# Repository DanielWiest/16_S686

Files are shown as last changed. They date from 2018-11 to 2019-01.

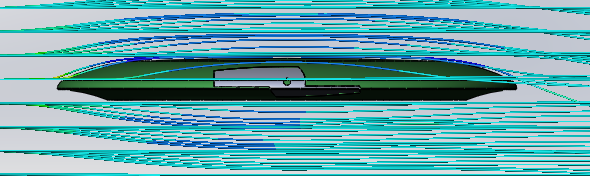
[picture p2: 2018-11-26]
Multimedia/Simulation_Renders/Port_Closed_Streamlines.PNG

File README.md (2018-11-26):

# __**16.S686**__ Closed Loop Frisbee Control
### A Repository of Code, Relevant Documents, and CAD Files

Frisbee Airflow

Surface Velocity

See subsections for more details.

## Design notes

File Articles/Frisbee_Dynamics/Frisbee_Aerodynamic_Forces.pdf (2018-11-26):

Physics 382, Student (2016) | Advanced Lab | v3.3, p.1

### Aerodynamics Forces on Frisbee

Karl Prasher and Professor Martin Madsen

Wabash College, 301 W. Wabash Ave, Crawfordsville, IN 47933

| (Dated: May 5, 2016)

The initial idea of the ultimate frisbee disc was first invented by Fred Morrison

in 1938 when him and his wife were tossing around an empty cake pan. Over the

years, Morrison developed several prototypes which eventually became the modern-

day ultimate disc. Richard Feynman modeled the disc as a ”wobbling plate” to

describe the motion of the frisbee [6]. The purpose of this experiment wasn’t to

model the motion of the disc but describe and explain the forces on a frisbee with

air drag.

I. INTRODUCTION

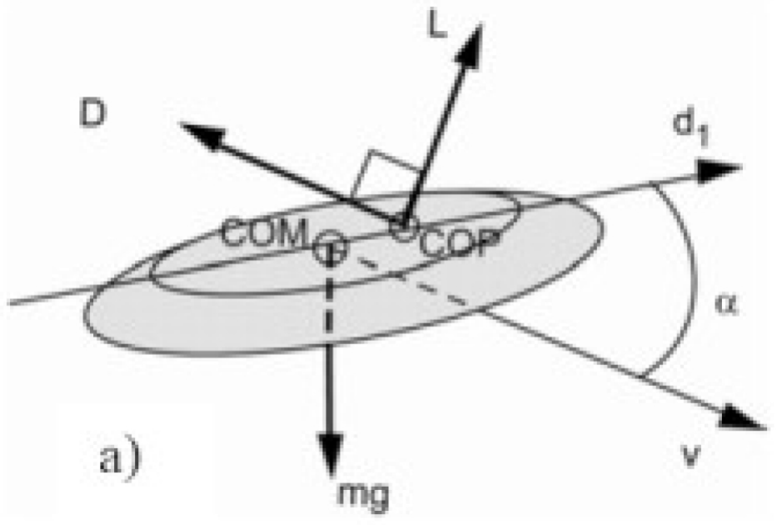
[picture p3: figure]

FIG. 1: This figure shows the setup procedure used during this experiment.

Richard Feynman once modeled the rotation and motion of a ”wobbling disc” similar

to an ultimate frisbee. He took moment of inertia, angular velocity, and angle of attack

into account. This model was just to describe the motion. This experiment took a different

approach and wanted to model the force on the frisbee changing the angle of attack therefore

changing the surface area as the frisbee travels through the air shown by Fig. . To model

the frisbee traveling through the air, a wind tunnel was built with a chamber able to insert

a pivot arm attached to the frisbee. Instead a modern-day 175 gram frisbee, we used an

mini-frisbee weighting approximately 28 grams.

II. SETUP

Fig. 2 shows the initial position of the system being tested. The initial trials began with

the pivot arm being at 90 degrees with relation to the x-axis. As the experiment continued,

the angle of the pivot arm was changed with respect to the x-axis called the attack angle.

Therefore, the surface area of the frisbee was changed ultimately changing the force on the

disc.

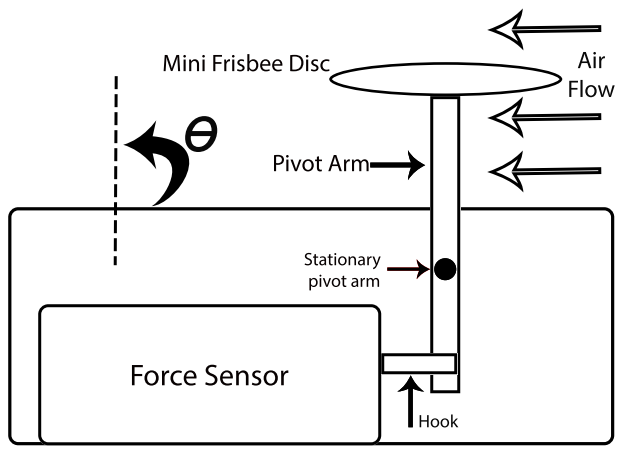
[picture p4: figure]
ForceSensor; MiniFrisbeeDisc; Stationary pivotarm; Air Flow; Hook; PivotArm

FIG. 2: This figure shows the setup procedure used during this experiment.

III. MODEL

Initially, the model relied on the rotation of the disc. Practicality though, there were

problems with a spinning disc inside the test chamber. Enabling the spinning motion was

not the problem, but measuring the force on the pivot arm while the disc was spinning was

the problem. It was not practical in my initial setup so the only variables that were changed

were the voltage powering the fan and the angle of attack. Then from Morrison’s paper, his

model was

Ftotal = Fdrag + Flif t, | (1)

but this experiment did not have the proper equipment to measure to the Lift Force so we

were left with only the Drag Force. Therefore my model came out to be

Fdrag = −

CDρAv²
2
, | (2)

where ρ is the density of air which is constant for this experiment, CD is a coefficient

determined by the physical attributes of the frisbee, and v is the velocity of the frisbee.

This follows the previous groups work that the model of the drag force should be close to a

quadratic fit model.

IV. DATA

My first task was to collect data over the same object as the previous group. By doing

this, it ensures that the equipment and model are up-to-date and works shown by Fig. 3.

This is shown in the analysis section with the curve fit.

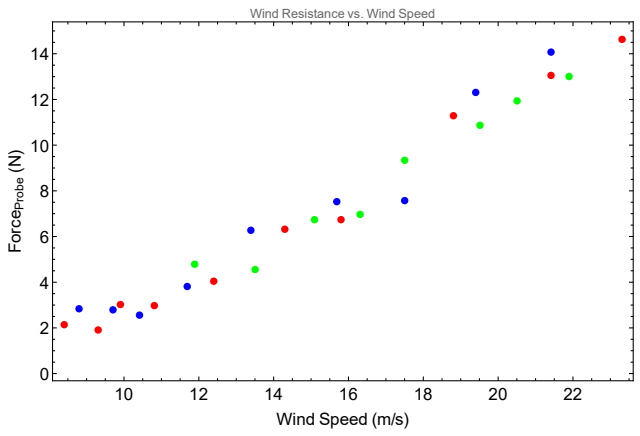
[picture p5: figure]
Wind Speed (m/s); ForceProbe (N); Wind Resistance vs. Wind Speed

FIG. 3: This plot shows the raw data over three trials of measuring the force upon the

racquetball.

Wind Resistance vs. Wind Speed on Mini Frisbee

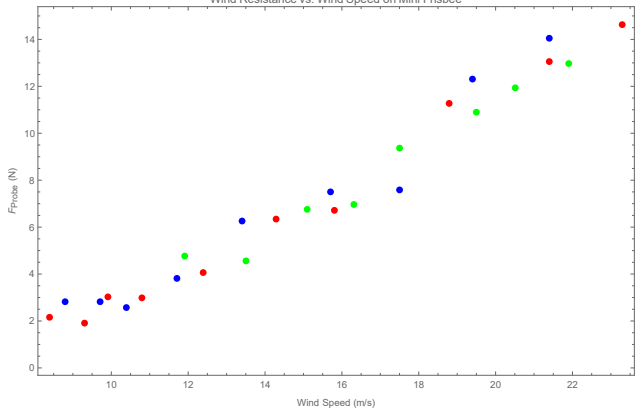
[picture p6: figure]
Wind Speed (m/s); FProbe (N)

FIG. 4: This plot shows the raw data over three trials of measuring the force upon the

mini frisbee.

Shown in Fig. 4, the data from the mini frisbee at 90 degrees was collected. During

those trials, only the voltage was changing. This shows a similar relationship of the force on

the mini frisbee as the racquetball. They both follow a parametric equation and this makes

sense with such a small cross-sectional area of the mini frisbee when it is as 90 degrees.

V. ANALYSIS

Based off Fig. 6, we were able to establish a clear relationship between the force of the

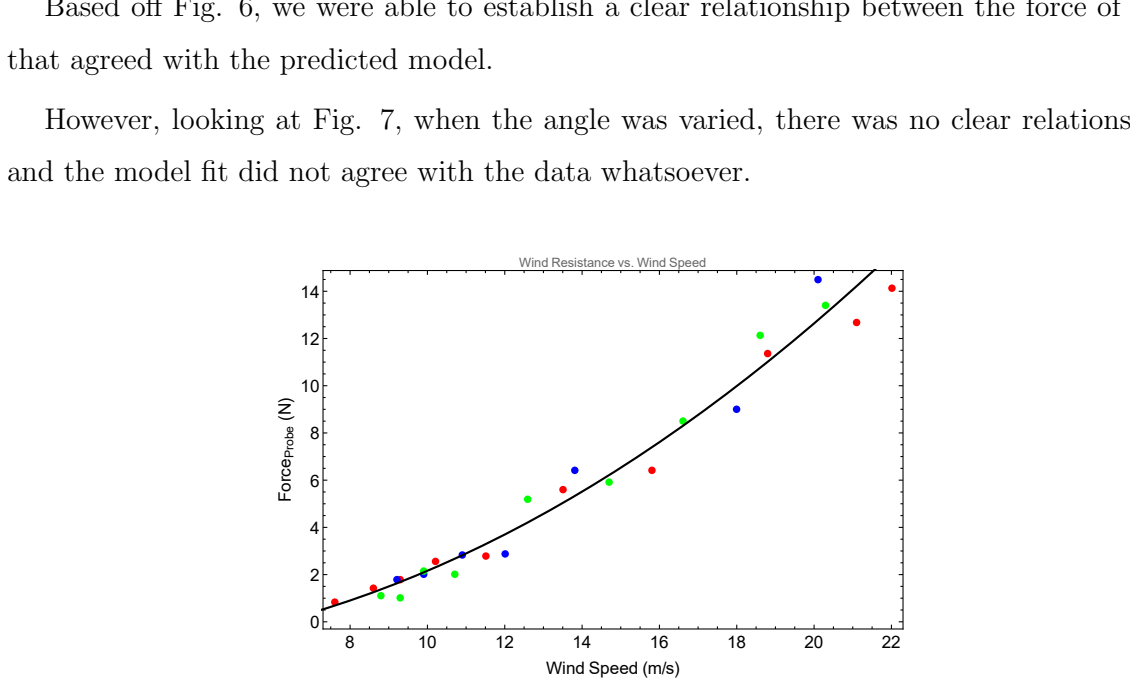
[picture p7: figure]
that agreed with the predicted model.; Wind Speed (m/s); ForceProbe (N); Wind Resistance vs. Wind Speed

However, looking at Fig. 7, when the angle was varied, there was no clear relationship

and the model fit did not agree with the data whatsoever.

FIG. 5: This plot shows the raw data over three trials of measuring the force upon the

racquetball.

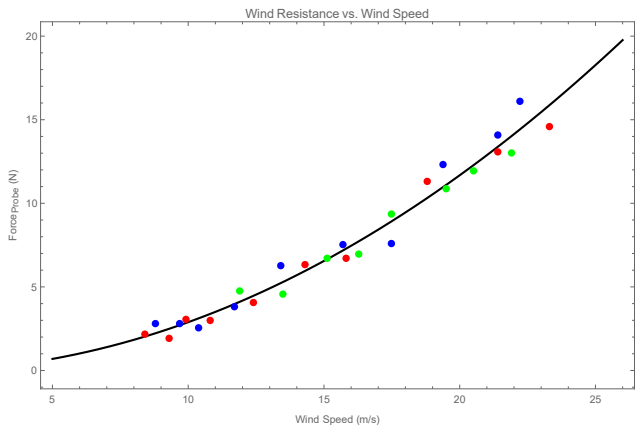
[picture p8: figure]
Wind Speed (m/s); ForceProbe (N); Wind Resistance vs. Wind Speed

FIG. 6: This plot shows a model with the three data sets of measuring the force upon the

mini frisbee.

74 | 76 | 78 | 80 | 82 | 84 | 86

2.0

2.2

2.4

2.6

2.8

3.0

Angle

FProbe on Mini Frisbee

{Angle of Attack vs. Force on Probe}

FIG. 7: This plot shows the raw data and model of measuring the drag force upon the

frisbee as the angle of attack was varied.

VI. CONCLUSION

Based on Fig. 6, a clear relationship between the Drag Force and the wind speed is

present but when the angle of attack of the frisbee (changing the cross sectional area of the

mini frisbee) is changed, there appears to be no relationship whatsoever. This could be due

to the setup of the mini frisbee yielding unreadable results. Further work should be done to

include the lift portion of the proper model of the total force on a rotating disc.

ACKNOWLEDGMENTS

We acknowledge the help and support of the Wabash College Physics Department.

[1] Baumback, K. “The Aerodynamics of Frisbee Flight.” Undergraduate Journal of Mathematical

Modeling: One Two UJMM: One Two, 3(1). (2013).

[2] Hubbard, M., & Cheng, K. B. “Optimal discus trajectories”. Journal of Biomechanics, 40(16),

3650-3659. (2007).

[3] Hummel, S. A. “Frisbee flight simulation and throw biomechanics.” (2003)
[4] Morrison, V. R. “The Physics of Frisbees.” Mount Allison University. (2005).
[5] Motoyama, E. “The Physics of Flying Discs.” (2002).

[6] Feynman, R.P. ”Surely You’re Joking, Mr. Feynman!”, New York: W. W. Norton, 1985 pp.

157158.

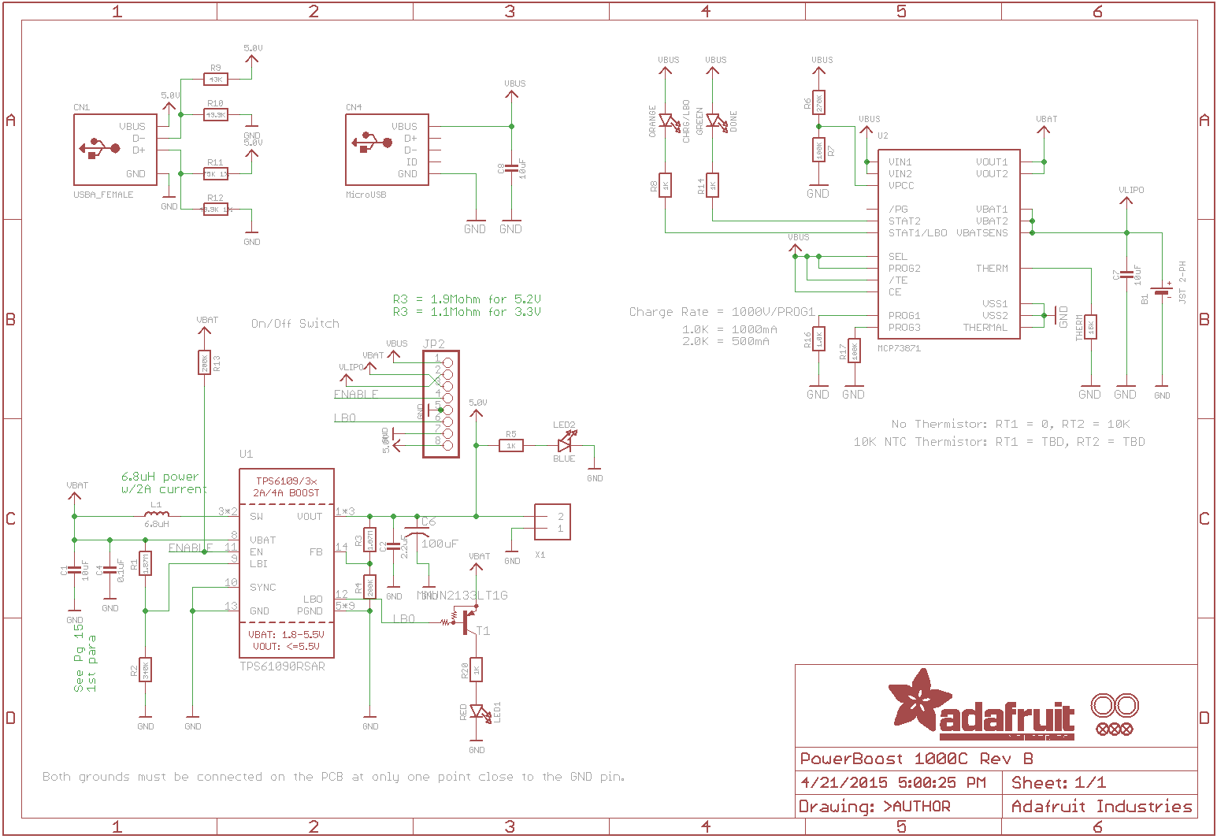
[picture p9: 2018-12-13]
Documents/PartSchematics/Powerboost.png

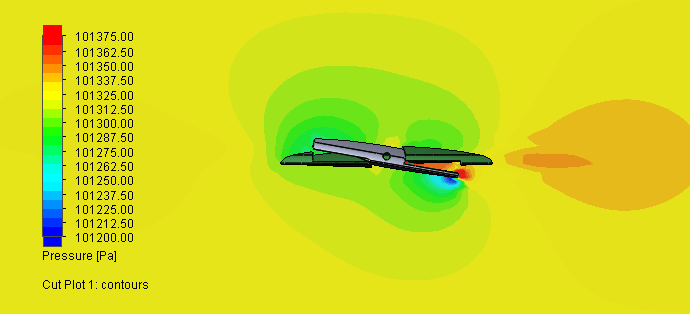
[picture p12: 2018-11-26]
Multimedia/Simulation_Renders/Port_Open_Pressure_Distribution.PNG

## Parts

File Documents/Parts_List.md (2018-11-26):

# Parts List

### 1. Solenoid Actuator:
Solenoid

Available [here](https://www.adafruit.com/product/2776) $4.95

### 2. Teensy 3.6 Microcontroller:
Teensy

Available [here](https://www.adafruit.com/product/3266) $29.95

### 3. Battery Charging and Voltage Regulation:
Boost + Regulator

Available [here](https://www.adafruit.com/product/2465) $19.95

### 4. Lithium Polymer Battery (500 mAh):
Battery

Available [here](https://www.adafruit.com/product/1578) $7.95

### 5. Hyperion High Speed Servo Actuator:
Hyperion Servo

Available [here](https://hyperion-world.com/en/p1772889-hp-ds09-gmd-14179) $11.86

### 6. Hyperion Servo Programming Adapter:
Programming Lead

Available [here](https://hyperion-world.com/en/p1770829-hp-at-prgusb) $13.90

### 7. Frisbee:
Frisbee

Available [here](https://www.amazon.com/Innova-Beast-Golf-Disc-Colors/dp/B00611XYXM) $13.90

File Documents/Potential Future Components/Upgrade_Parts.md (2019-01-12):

# Parts List

### SERVO Saver:


The impact of hitting the ground would likely strip the servo's gearing without any sort of protection.

Available [here](https://www.amazon.com/Hot-Racing-SHS88H-Aluminum-Vehicle/dp/B00A29B2D8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)

### 2. Teensy 3.6 Microcontroller:

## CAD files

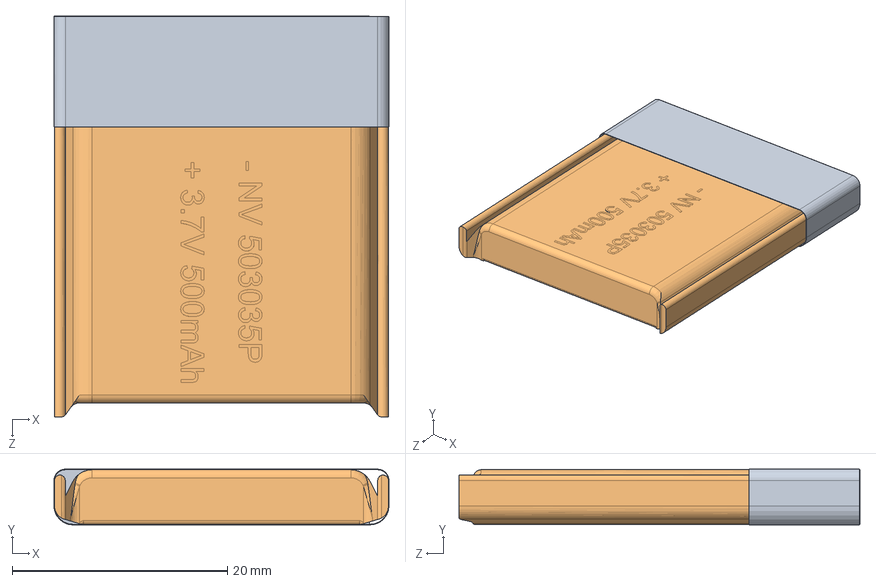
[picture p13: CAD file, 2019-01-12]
CAD/Battery/500mAh Battery.SLDASM
31.1 x 5.17 x 37.2 mm
Kapton Tape
Battery Cell
Board Part 1
PCB
Board Part 2

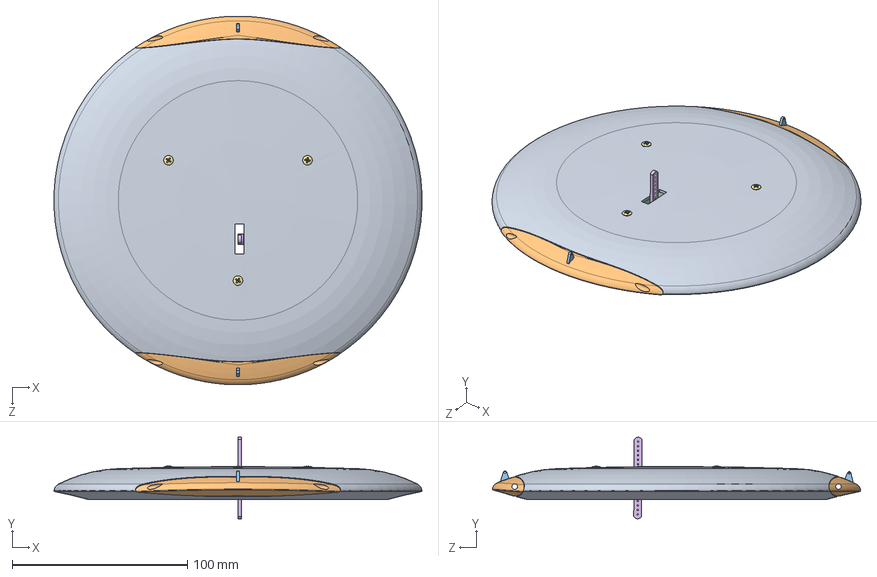
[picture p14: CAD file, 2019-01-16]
CAD/TopLevelAllComponents.SLDASM
209.8 x 46.5 x 210.0 mm
Frisbee_with_control_cutout_linear_v2
linear_control_surface_v1 x 2
ControlHorn x 2
Kapton Tape
Battery Cell
Board Part 1
PCB
Board Part 2
Adafruit_BNO055
Teensy 3.6
PowerBoost1000C
ElectronicsEnclosure
DS09GMD
long_control_horn
oval head_am x 3

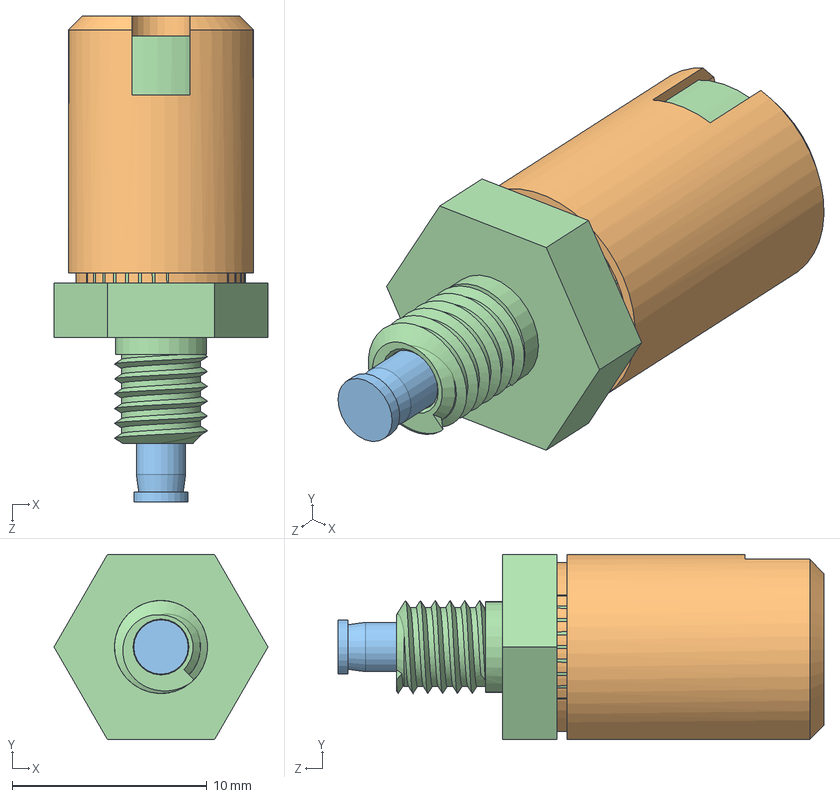
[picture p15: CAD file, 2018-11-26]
CAD/Solenoids/Solenoid_CAD_alternative_option.sldasm
11.0 x 9.53 x 25.0 mm
SPRING_Default
HOUSING_Default
PLUNGER_Default
Swing bolt_Default

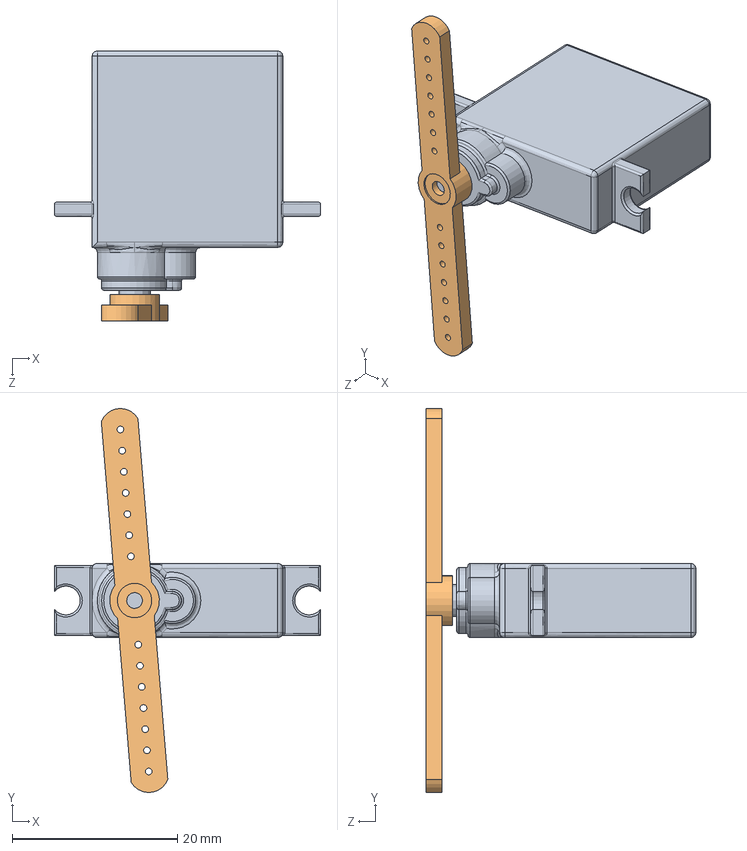
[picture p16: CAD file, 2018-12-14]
CAD/Servo/ServoAssem.SLDASM
32.2 x 46.4 x 32.6 mm
DS09GMD
long_control_horn

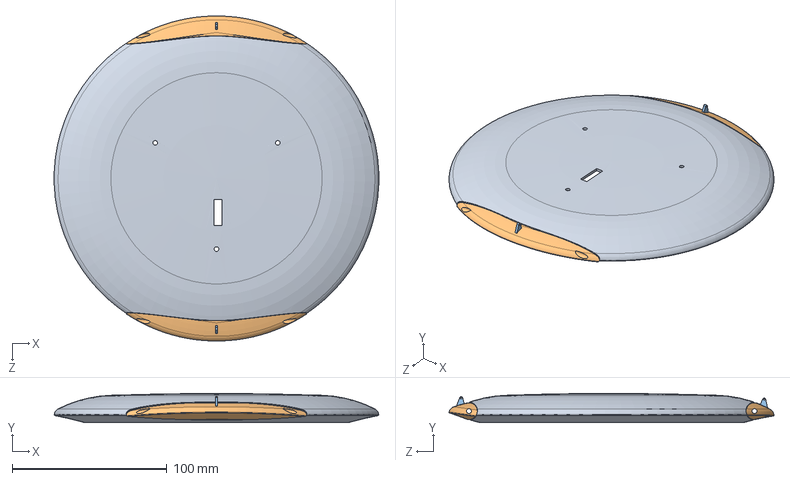
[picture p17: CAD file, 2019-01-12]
CAD/Top_level_assembly_v2.SLDASM
209.8 x 18.8 x 210.0 mm
Frisbee_with_control_cutout_linear_v2
linear_control_surface_v1 x 2
ControlHorn x 2

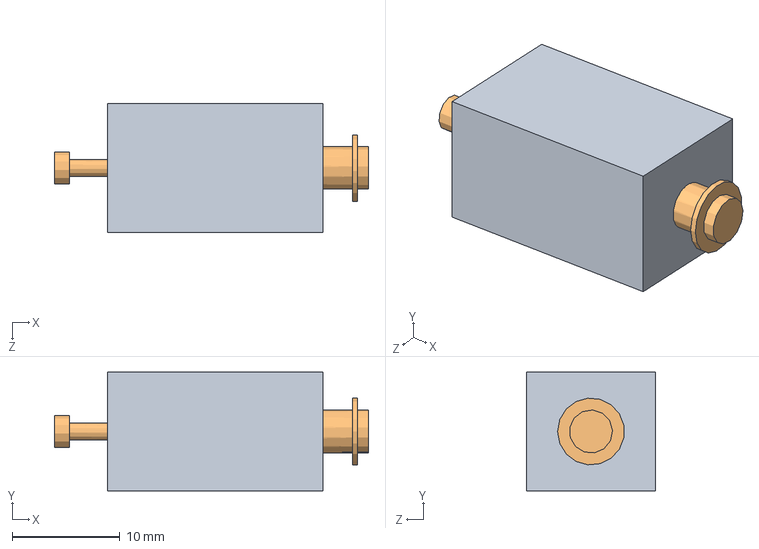
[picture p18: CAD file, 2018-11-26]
CAD/Solenoids/microSolenoidAssembly.SLDASM
29.1 x 11.0 x 12.0 mm
Pin

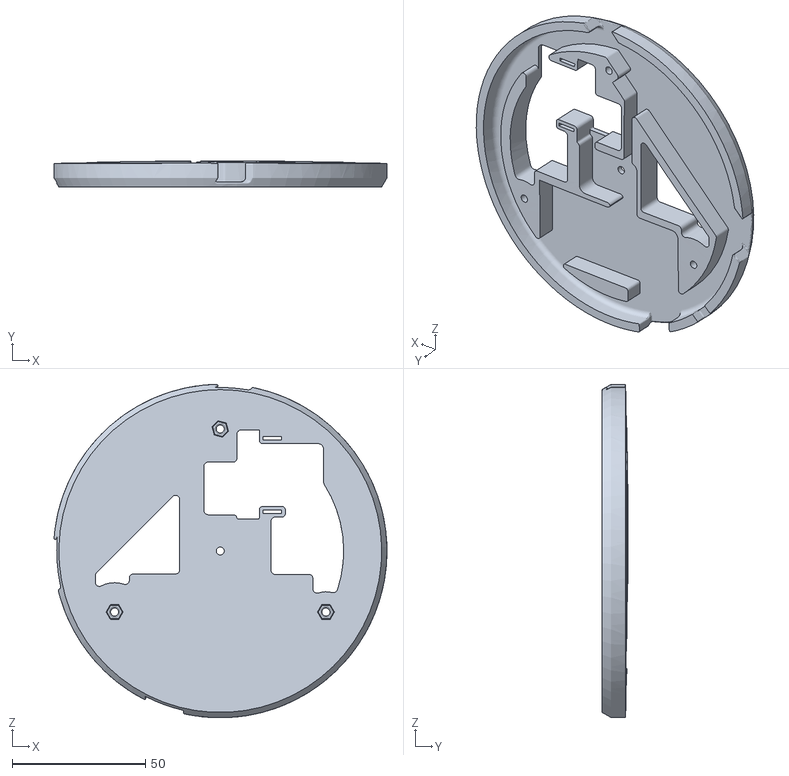
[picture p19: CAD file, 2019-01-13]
CAD/3D Printing Files/ElectronicsEnclosureTEST.STL
124.8 x 9.85 x 124.9

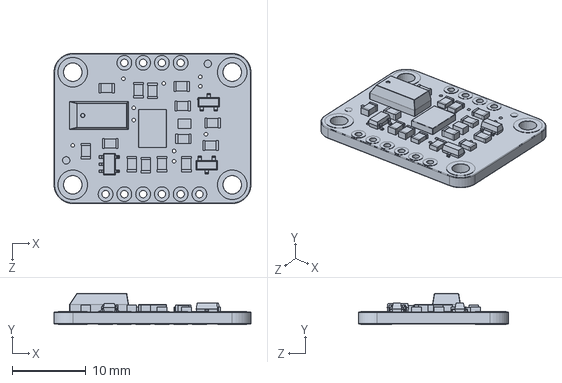
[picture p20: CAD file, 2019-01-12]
CAD/BNO005/Adafruit_BNO055.SLDPRT
26.7 x 4.20 x 20.3 mm

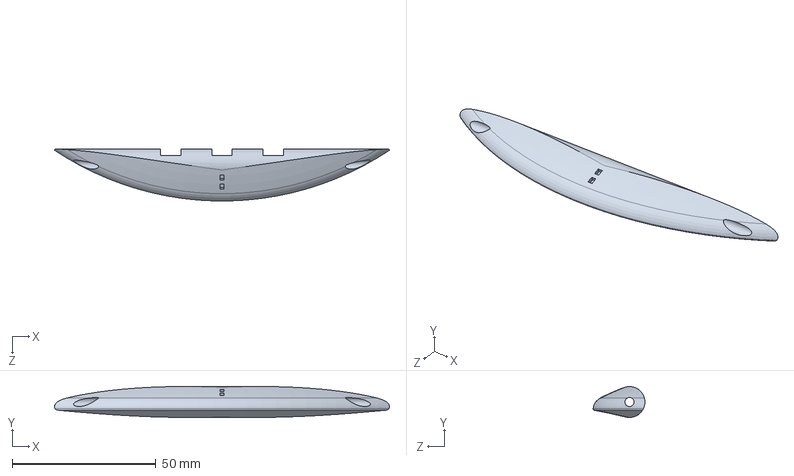
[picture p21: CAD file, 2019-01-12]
CAD/Control_Surfaces/linear_control_surface_v1.sldprt
116.7 x 10.8 x 18.1 mm

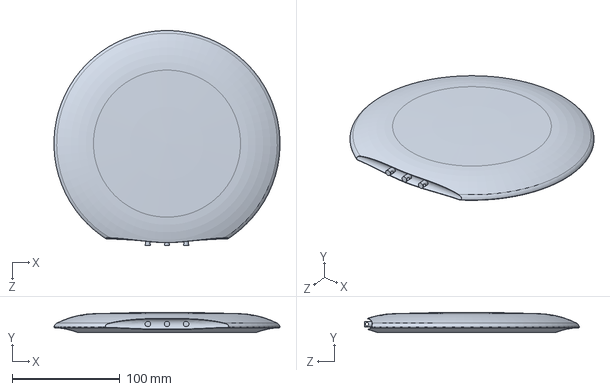
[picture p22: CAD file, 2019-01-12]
CAD/Frisbee/Frisbee_with_control_cutout_linear_v2.SLDPRT
209.8 x 18.8 x 199.4 mm

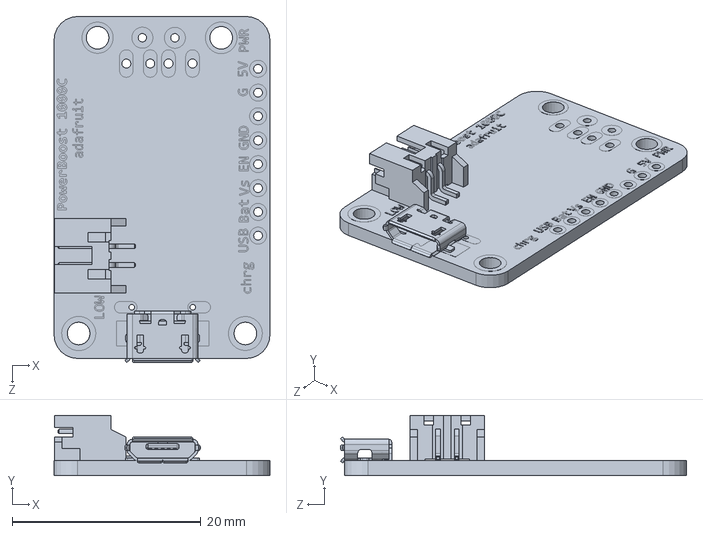
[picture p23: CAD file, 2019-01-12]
CAD/PowerBoost 1000C/PowerBoost1000C.SLDPRT
22.9 x 6.39 x 36.6 mm

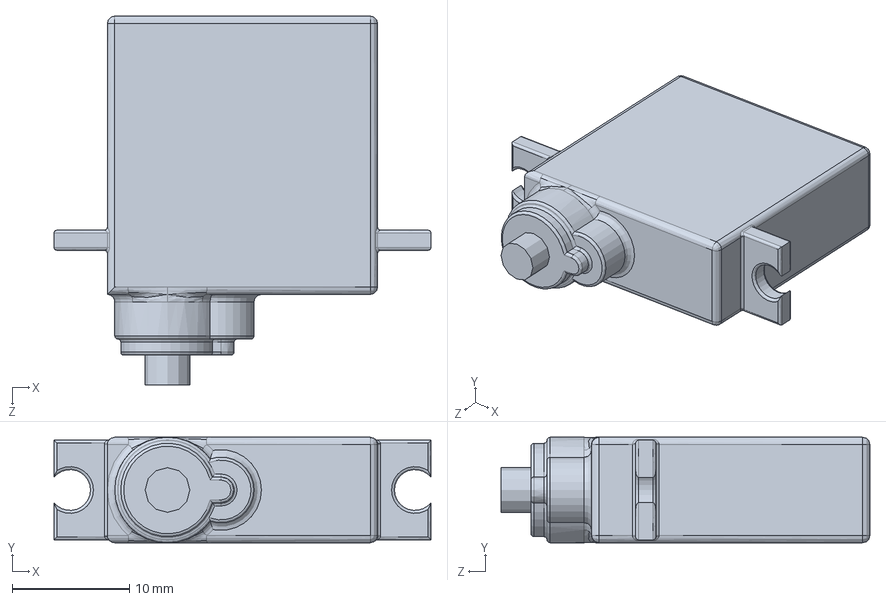
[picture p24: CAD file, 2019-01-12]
CAD/Servo/DS09GMD.SLDPRT
32.2 x 9.00 x 31.5 mm

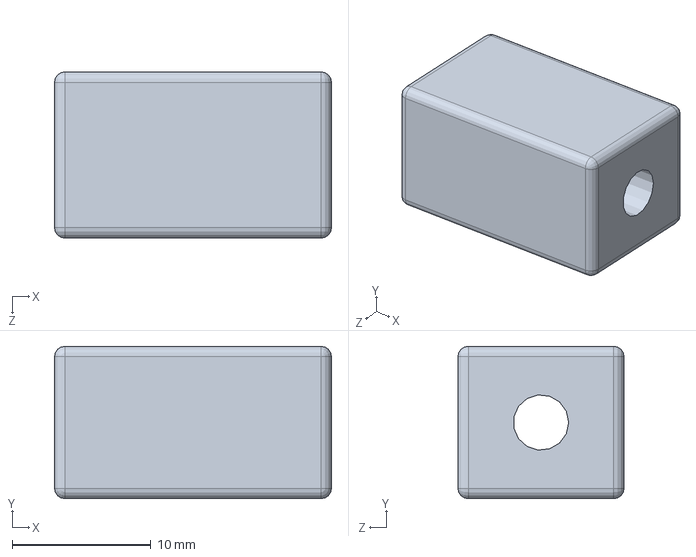
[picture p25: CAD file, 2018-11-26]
CAD/Solenoids/Body.SLDPRT
20.0 x 11.0 x 12.0 mm

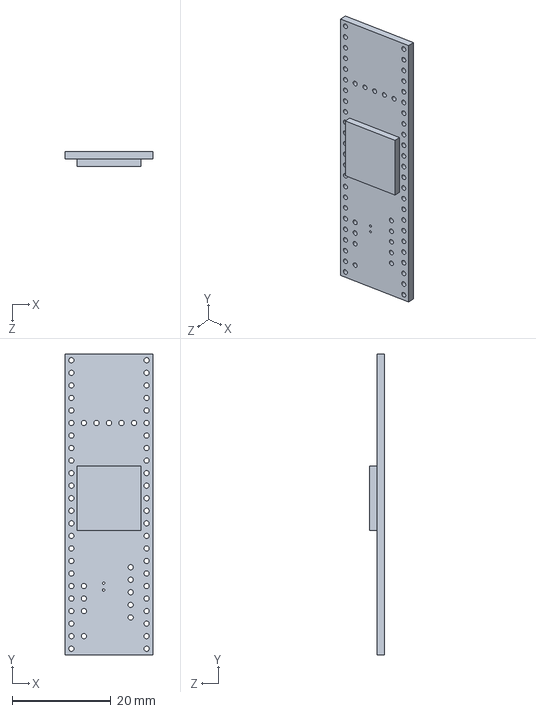
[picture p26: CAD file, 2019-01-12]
CAD/Teensy/Teensy 3.6.SLDPRT
17.8 x 61.0 x 3.10 mm

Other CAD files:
CAD/Battery/Battery Cell.sldprt
CAD/Control_Surfaces/ControlHorn.sldprt
CAD/ElectronicsEnclosure.sldprt
CAD/Frisbee/Unaltered_disc.SLDPRT
CAD/Battery/Board Part 1.sldprt
CAD/Battery/Board Part 2.sldprt
CAD/Battery/Kapton Tape.sldprt
CAD/Battery/PCB.sldprt
CAD/Control_Surfaces/Control_surface_v2.sldprt
CAD/Frisbee/Frisbee_with_control_cutout.SLDPRT
CAD/Servo/long_control_horn.SLDPRT
CAD/Solenoids/Pin.SLDPRT
CAD/Top_level_assembly.SLDASM

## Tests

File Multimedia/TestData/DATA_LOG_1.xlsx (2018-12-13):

Time | Euler_x | Euler_y | Euler_z | Grav_x | Grav_y | Grav_z | LinAcc_x | LinAcc_y | LinAcc_z | Control_Setpoint
1234 | 0 | 0 | 0 | 0 | 0 | 0 | 0 | 0 | 0 | 0
1245 | 2.75 | 5.44 | -2.12 | 0.93 | 0.36 | 9.75 | -4.1 | -1.98 | -2.69 | 0
1256 | 3.25 | 6.62 | -2.88 | 1.13 | 0.49 | 9.72 | -4.27 | -1.76 | -3.52 | 0
1267 | 3.88 | 8 | -3.94 | 1.37 | 0.67 | 9.68 | -4.13 | -1.47 | -3.78 | 0
1282 | 4.56 | 9.56 | -5.31 | 1.63 | 0.89 | 9.62 | -3.22 | -0.76 | -2.7 | 0
1293 | 5.25 | 11.19 | -6.81 | 1.91 | 1.14 | 9.54 | -2.37 | -0.78 | -1.01 | 0
1305 | 6.69 | 14.56 | -10 | 2.47 | 1.65 | 9.34 | -2.22 | -0.83 | -0.41 | 0
1316 | 7.38 | 16.25 | -11.44 | 2.74 | 1.87 | 9.22 | -1.21 | -1.07 | 1.06 | 0
1327 | 8 | 17.81 | -12.62 | 3 | 2.04 | 9.1 | -1.08 | -1.26 | 1.6 | 0
1338 | 8.5 | 19.31 | -13.69 | 3.24 | 2.19 | 8.98 | -1.29 | -1.29 | 1.65 | 0
1353 | 9.06 | 20.69 | -14.62 | 3.47 | 2.31 | 8.87 | -1.55 | -1.06 | 0.02 | 0
1365 | 10.06 | 23.44 | -16.69 | 3.9 | 2.59 | 8.61 | -1.56 | -1.01 | 0.2 | 0
1377 | 10.62 | 24.75 | -18 | 4.1 | 2.76 | 8.46 | -1.43 | -1.03 | 0.65 | 0
1389 | 11.12 | 25.94 | -19.5 | 4.29 | 2.95 | 8.3 | -1.13 | -1.03 | 1.37 | 0
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

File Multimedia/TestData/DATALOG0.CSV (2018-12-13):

Time | Euler_x | Euler_y | Euler_z | Grav_x | Grav_y | Grav_z | LinAcc_x | LinAcc_y | LinAcc_z | Control_Setpoint
1143 | 0.00 | 0.00 | 0.00 | 0.00 | 0.00 | 0.00 | 0.00 | 0.00 | 0.00 | 0.00
1154 | 0.00 | 0.00 | 0.00 | 0.00 | 0.00 | 0.00 | 0.00 | 0.00 | 0.00 | 0.00
1166 | 0.00 | 0.00 | 0.00 | 0.00 | 0.00 | 0.00 | 0.00 | 0.00 | 0.00 | 0.00
1177 | 0.00 | 0.00 | 0.00 | 0.00 | 0.00 | 0.00 | 0.00 | 0.00 | 0.00 | 0.00
1289 | 0.00 | 0.00 | 0.00 | 0.00 | 0.00 | 0.00 | 0.00 | 0.00 | 0.00 | 0.00
1300 | 0.00 | 0.00 | 0.00 | 0.00 | 0.00 | 0.00 | 0.00 | 0.00 | 0.00 | 0.00
1312 | 0.00 | 0.00 | 0.00 | 0.00 | 0.00 | 0.00 | 0.00 | 0.00 | 0.00 | 0.00
1324 | 0.00 | 0.00 | 0.00 | 0.00 | 0.00 | 0.00 | 0.00 | 0.00 | 0.00 | 0.00
1335 | 0.00 | 0.00 | 0.00 | 0.00 | 0.00 | 0.00 | 0.00 | 0.00 | 0.00 | 0.00
1346 | 0.00 | 0.00 | 0.00 | 0.00 | 0.00 | 0.00 | 0.00 | 0.00 | 0.00 | 0.00
1358 | 0.00 | 0.00 | 0.00 | 0.00 | 0.00 | 0.00 | 0.00 | 0.00 | 0.00 | 0.00
1369 | 0.00 | 0.00 | 0.00 | 0.00 | 0.00 | 0.00 | 0.00 | 0.00 | 0.00 | 0.00
1383 | 0.00 | 0.00 | 0.00 | 0.00 | 0.00 | 0.00 | 0.00 | 0.00 | 0.00 | 0.00
1394 | 0.00 | 0.00 | 0.00 | 0.00 | 0.00 | 0.00 | 0.00 | 0.00 | 0.00 | 0.00
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

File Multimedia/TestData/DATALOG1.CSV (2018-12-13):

Time | Euler_x | Euler_y | Euler_z | Grav_x | Grav_y | Grav_z | LinAcc_x | LinAcc_y | LinAcc_z | Control_Setpoint
1949 | 0.00 | 0.00 | 0.00 | 0.00 | 0.00 | 0.00 | 0.00 | 0.00 | 0.00 | 0.00
1961 | 0.00 | 0.00 | 0.00 | 0.00 | 0.00 | 0.00 | 0.00 | 0.00 | 0.00 | 0.00
1973 | 0.00 | 0.00 | 0.00 | 0.00 | 0.00 | 0.00 | 0.00 | 0.00 | 0.00 | 0.00
1984 | 0.00 | 0.00 | 0.00 | 0.00 | 0.00 | 0.00 | 0.00 | 0.00 | 0.00 | 0.00
1996 | 0.00 | 0.00 | 0.00 | 0.00 | 0.00 | 0.00 | 0.00 | 0.00 | 0.00 | 0.00
2008 | 0.00 | 0.00 | 0.00 | 0.00 | 0.00 | 0.00 | 0.00 | 0.00 | 0.00 | 0.00
2020 | 0.00 | 0.00 | 0.00 | 0.00 | 0.00 | 0.00 | 0.00 | 0.00 | 0.00 | 0.00
2031 | 0.00 | 0.00 | 0.00 | 0.00 | 0.00 | 0.00 | 0.00 | 0.00 | 0.00 | 0.00
2042 | 0.00 | 0.00 | 0.00 | 0.00 | 0.00 | 0.00 | 0.00 | 0.00 | 0.00 | 0.00
2054 | 0.00 | 0.00 | 0.00 | 0.00 | 0.00 | 0.00 | 0.00 | 0.00 | 0.00 | 0.00
2066 | 0.00 | 0.00 | 0.00 | 0.00 | 0.00 | 0.00 | 0.00 | 0.00 | 0.00 | 0.00
2078 | 0.00 | 0.00 | 0.00 | 0.00 | 0.00 | 0.00 | 0.00 | 0.00 | 0.00 | 0.00
2089 | 0.00 | 0.00 | 0.00 | 0.00 | 0.00 | 0.00 | 0.00 | 0.00 | 0.00 | 0.00
2101 | 0.00 | 0.00 | 0.00 | 0.00 | 0.00 | 0.00 | 0.00 | 0.00 | 0.00 | 0.00
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

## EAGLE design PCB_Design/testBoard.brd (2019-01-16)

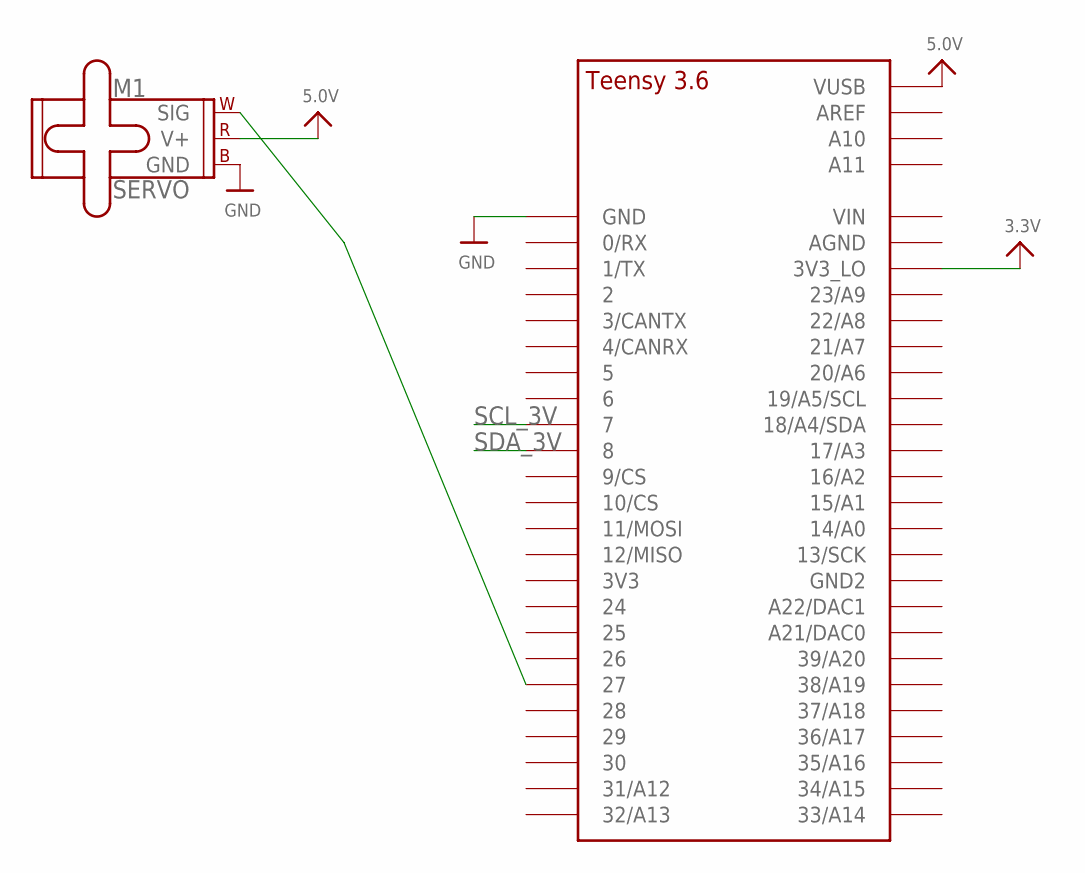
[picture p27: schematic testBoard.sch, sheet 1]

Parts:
M1: SERVO; 1X03
U$69: TEENSY_3.5/3.6_BASIC

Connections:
3.3V: U$69.3V3_LO; also elsewhere on the board
5.0V: M1.2 (V+), U$69.VUSB; also elsewhere on the board
GND: M1.3 (GND), U$69.GND; also elsewhere on the board
unnamed: M1.1 (SIG), U$69.27
SCL_3V: U$69.7; also elsewhere on the board
SDA_3V: U$69.8; also elsewhere on the board

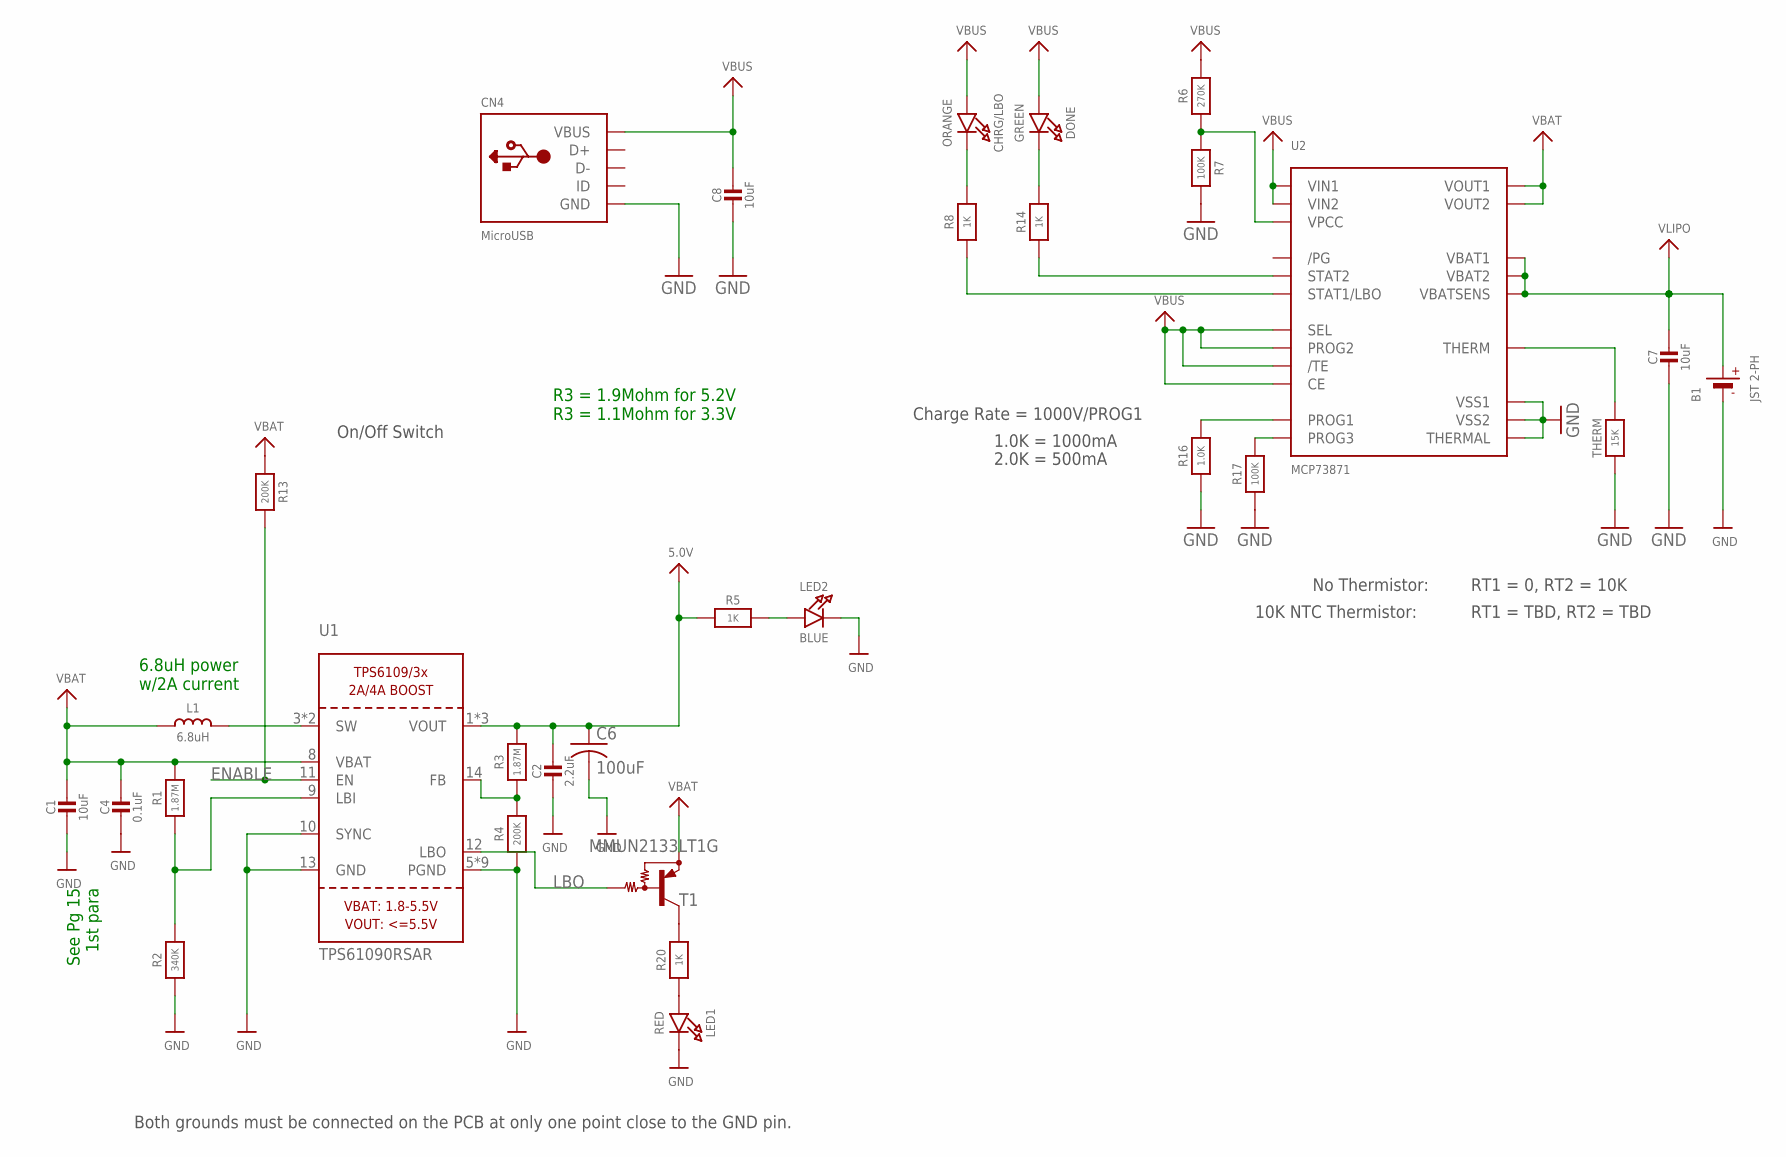
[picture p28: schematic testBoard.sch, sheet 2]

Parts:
B1: JST 2-PH; JSTPH2
C1, C7, C8: 10uF; 0805-NO
C2: 2.2uF; 0805-NO
C4: 0.1uF; 0805_10MGAP
C6: 100uF; C1210
CHRG/LBO: ORANGE; CHIPLED_0805_NOOUTLINE
CN4: MicroUSB; 4UCONN_20329
DONE: GREEN; CHIPLED_0805_NOOUTLINE
L1: 6.8uH; INDUCTOR_5X5MM_TDK_VLC5045
LED1: RED; CHIPLED_0805_NOOUTLINE
LED2: BLUE; CHIPLED_0805_NOOUTLINE
R1: 1.87M; _0805MP
R2: 340K; _0805MP
R3: 1.87M; 0805-NO
R4, R13: 200K; 0805-NO
R5, R8, R14, R20: 1K; 0805-NO
R6: 270K; 0805-NO
R7, R17: 100K; 0805-NO
R16: 1.0K; 0805-NO
T1: MMUN2133LT1G; SC59-BEC
THERM: 15K; 0805-NO
U1: TPS61090RSAR; PVQFN-16
U2: MCP73871; QFN20_4MM

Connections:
5.0V: C2.1, C6.1, R3.2, R5.1, U1.1 (VOUT), U1.15 (VOUT), U1.16 (VOUT); also elsewhere on the board
ENABLE: R13.2, U1.11 (EN)
GND: B1.1 (-), C1.2, C2.2, C4.2, C6.2, C7.2, C8.2, CN4.BASE@1 (GND), CN4.BASE@2 (GND), CN4.GND, CN4.SPRT@1 (GND), CN4.SPRT@2 (GND), CN4.SPRT@3 (GND), CN4.SPRT@4 (GND), LED1.C, LED2.C, R2.1, R4.1, R7.2, R16.1, R17.1, THERM.1, U1.5 (PGND), U1.6 (PGND), U1.7 (PGND), U1.10 (SYNC), U1.13 (GND), U1.P$18 (PGND), U1.P$19 (PGND), U1.P$20 (PGND), U1.P$21 (PGND), U1.P$22 (PGND), U1.THERMAL (PGND), U2.P$10 (VSS1), U2.P$11 (VSS2), U2.P$21 (THERMAL); also elsewhere on the board
LBO: T1.B, U1.12 (LBO)
unnamed: L1.P$2 (2), U1.3 (SW), U1.4 (SW)
unnamed: LED1.A, R20.1
unnamed: R1.1, R2.2, U1.9 (LBI)
unnamed: LED2.A, R5.2
unnamed: R3.1, R4.2, U1.14 (FB)
unnamed: R20.2, T1.C
unnamed: R6.1, R7.1, U2.P$2 (VPCC)
unnamed: DONE.C, R14.2
unnamed: R14.1, U2.P$7 (STAT2)
unnamed: THERM.2, U2.P$5 (THERM)
unnamed: R8.1, U2.P$8 (STAT1/LBO)
unnamed: CHRG/LBO.C, R8.2
unnamed: R17.2, U2.P$12 (PROG3)
unnamed: R16.2, U2.P$13 (PROG1)
VBAT: C1.1, C4.1, L1.P$1 (1), R1.2, R13.1, T1.E, U1.8 (VBAT), U2.P$1 (VOUT1), U2.P$20 (VOUT2)
VBUS: C8.1, CHRG/LBO.A, CN4.VBUS, DONE.A, R6.2, U2.P$3 (SEL), U2.P$4 (PROG2), U2.P$9 (/TE), U2.P$17 (CE), U2.P$18 (VIN1), U2.P$19 (VIN2)
VLIPO: B1.2 (+), C7.1, U2.P$14 (VBAT1), U2.P$15 (VBAT2), U2.P$16 (VBATSENS)

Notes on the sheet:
Both grounds must be connected on the PCB at only one point close to the GND pin.
On/Off Switch
See Pg 15 1st para
6.8uH power w/2A current
R3 = 1.9Mohm for 5.2V R3 = 1.1Mohm for 3.3V
Charge Rate = 1000V/PROG1
1.0K = 1000mA
2.0K = 500mA
No Thermistor:
10K NTC Thermistor:
RT1 = 0, RT2 = 10K
RT1 = TBD, RT2 = TBD

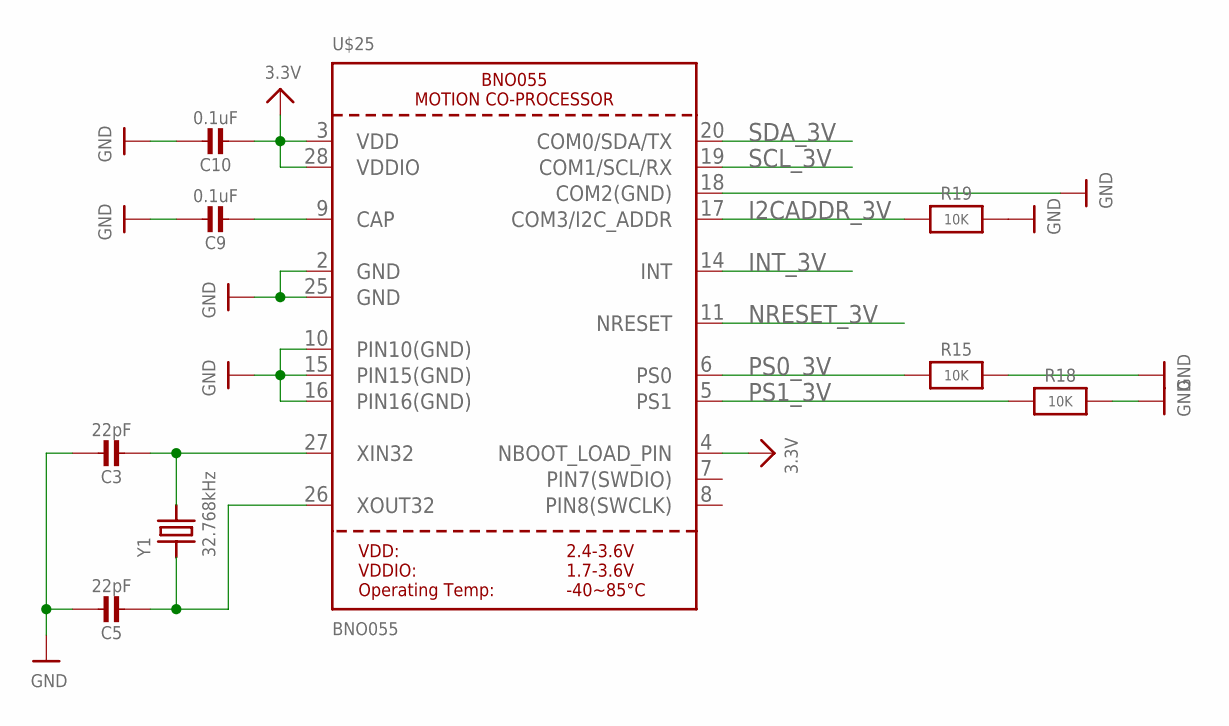
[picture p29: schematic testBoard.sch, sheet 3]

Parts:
C3, C5: 22pF; 0805-NO
C9: 0.1uF; 0805-NO
C10: 0.1uF; 0805_10MGAP
R15, R18, R19: 10K; 0805-NO
U$25: BNO055
Y1: 32.768kHz; CRYSTAL_8X3.8

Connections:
3.3V: C10.2, U$25.3 (VDD), U$25.4 (NBOOT_LOAD_PIN), U$25.28 (VDDIO); also elsewhere on the board
GND: C3.1, C5.1, C9.1, C10.1, R15.2, R18.2, R19.2, U$25.2 (GND), U$25.10 (PIN10(GND)), U$25.15 (PIN15(GND)), U$25.16 (PIN16(GND)), U$25.18 (COM2(GND)), U$25.25 (GND); also elsewhere on the board
I2CADDR_3V: R19.1, U$25.17 (COM3/I2C_ADDR)
INT_3V: U$25.14 (INT)
unnamed: C3.2, U$25.27 (XIN32), Y1.P$4 (2)
unnamed: C5.2, U$25.26 (XOUT32), Y1.P$1 (1)
unnamed: C9.2, U$25.9 (CAP)
NRESET_3V: U$25.11 (NRESET)
PS0_3V: R15.1, U$25.6 (PS0)
PS1_3V: R18.1, U$25.5 (PS1)
SCL_3V: U$25.19 (COM1/SCL/RX); also elsewhere on the board
SDA_3V: U$25.20 (COM0/SDA/TX); also elsewhere on the board

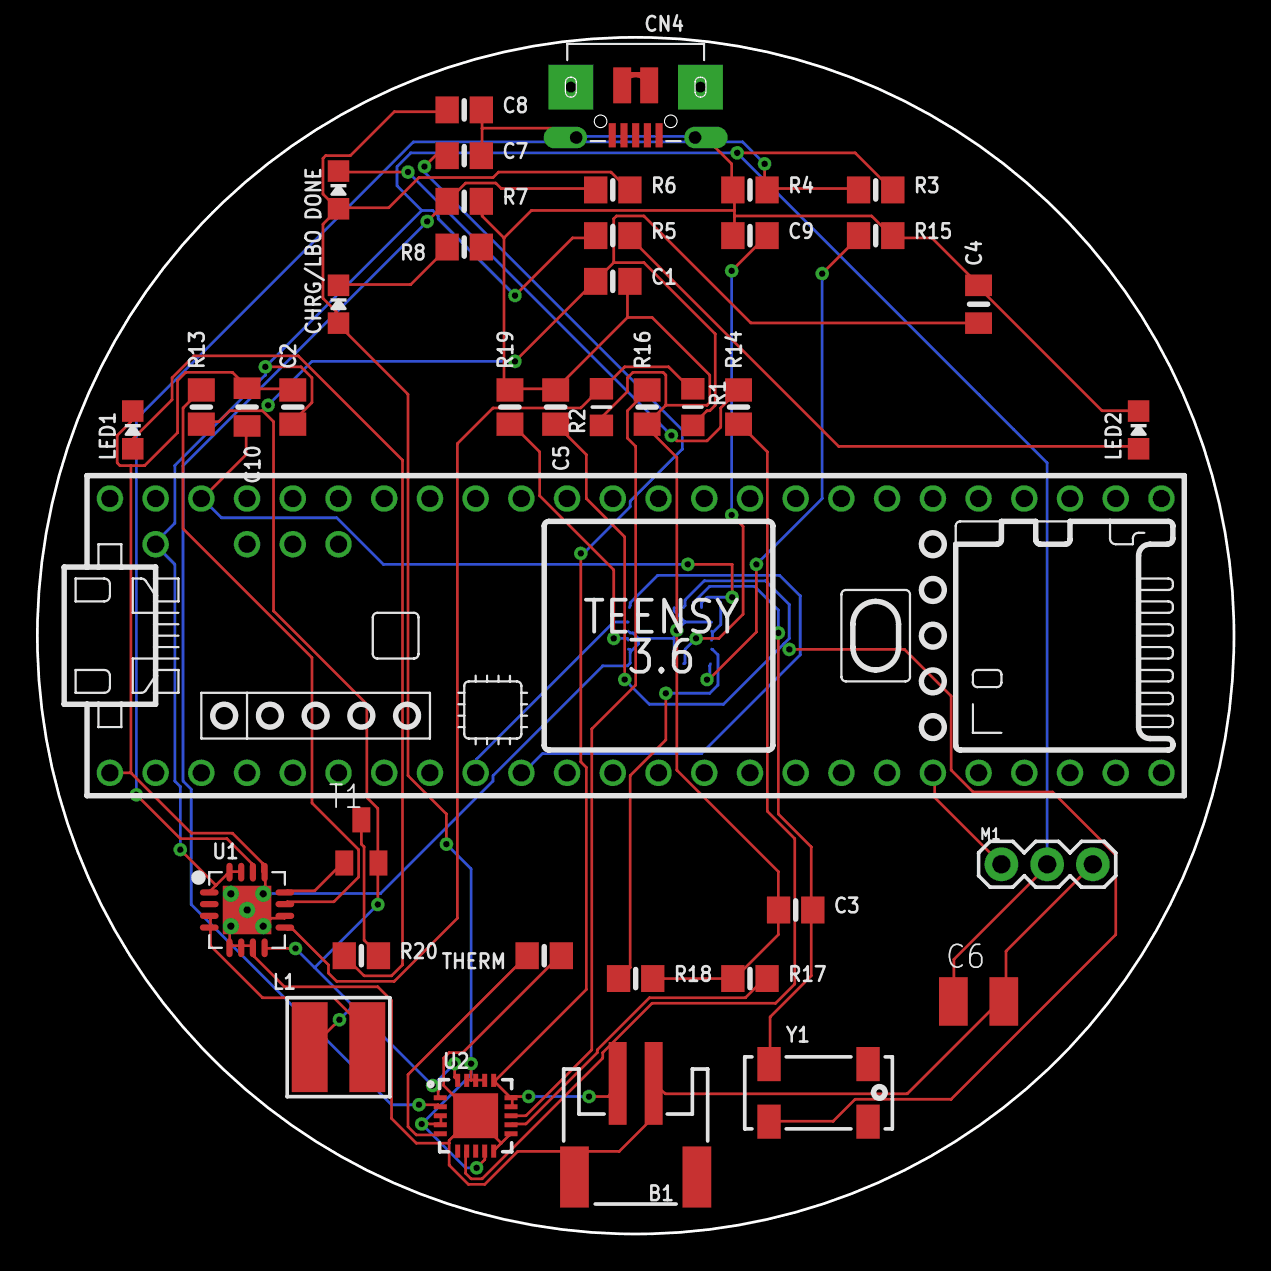
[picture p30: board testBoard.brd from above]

Board: 2 copper layers, 66.5 x 66.5 mm, 41 parts (1 on the bottom side), 31 nets.

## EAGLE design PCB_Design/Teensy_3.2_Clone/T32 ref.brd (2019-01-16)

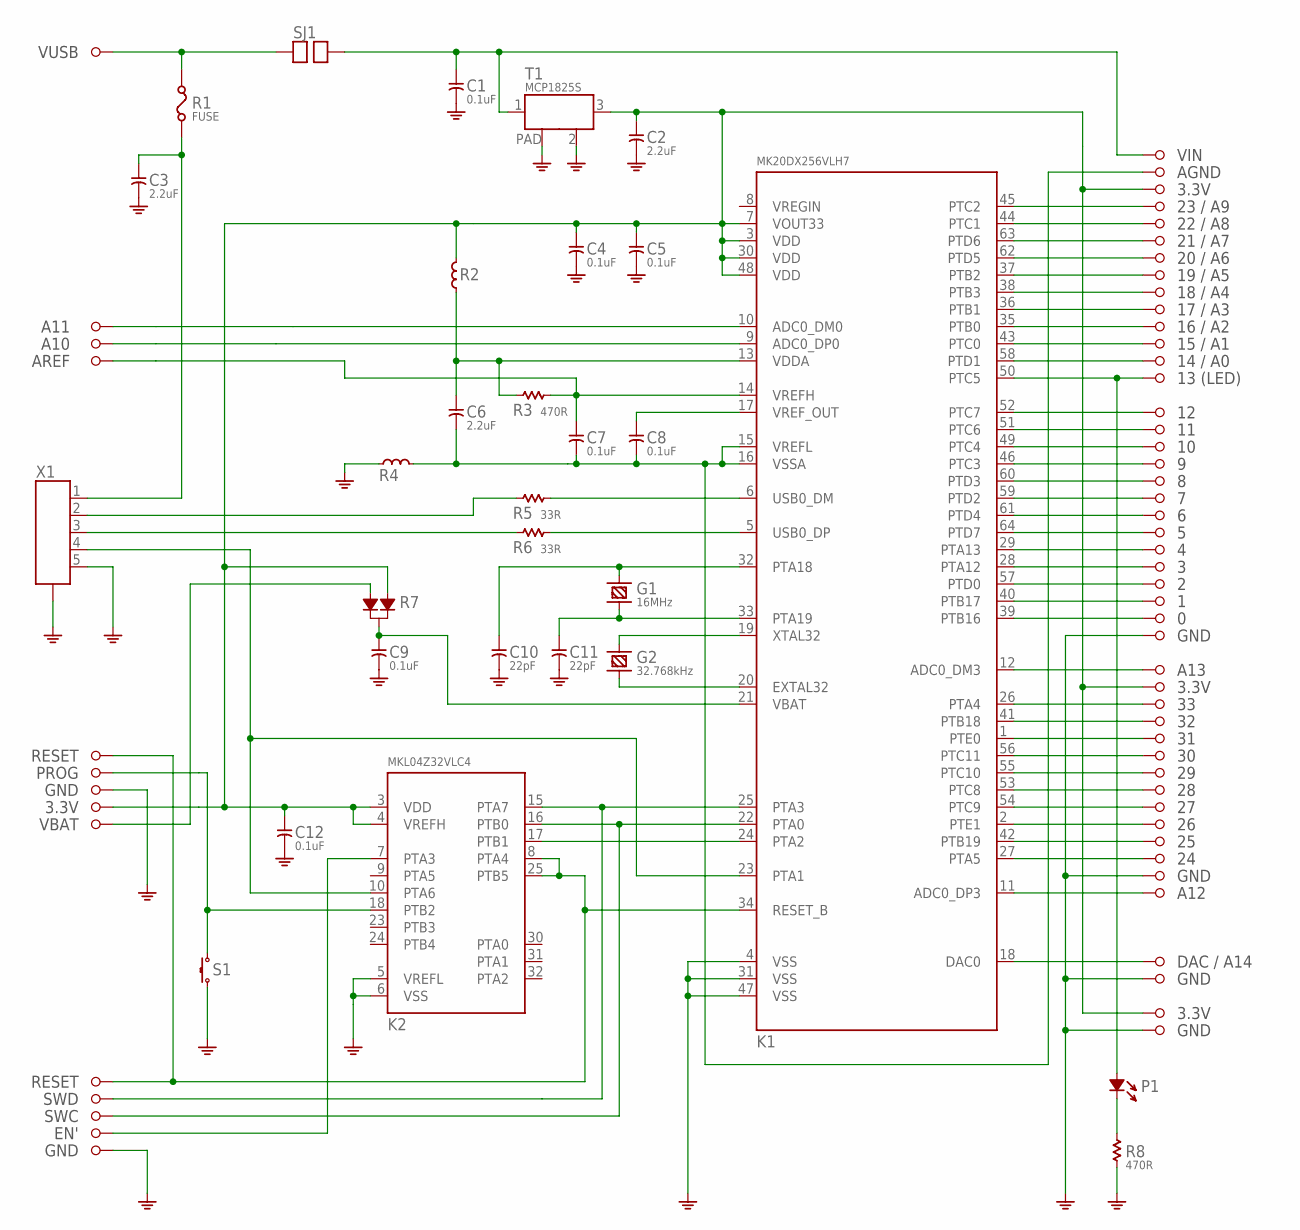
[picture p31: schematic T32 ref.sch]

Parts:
C1, C4, C5, C7, C8, C9, C12: 0.1uF; C0603
C2, C3, C6: 2.2uF; C0805
C10, C11: 22pF; C0603
G1: 16MHz; HC49US
G2: 32.768kHz; TC26H
K1: MK20DX256VLH7; LQFP64-05
K2: MKL04Z32VLC4; LQFP32-08
P1: LED; LED-0805
R1: FUSE; F0805
R2, R4: FERRITE; L0603
R3, R8: 470R; R0603
R5, R6: 33R; R0603
R7: DIODE_DUAL; SOT-23
S1: TACT_SWITCH; ALPS_SKHH
SJ1: SOLDERJUMPER
SX1, SX2, SX3, SX4, SX5, SX6, SX7, SX8, SX9, SX10, SX11, SX12, SX13, SX14, SX15, SX16, SX17, SX18, SX19, SX20, SX21, SX22, SX23, SX24, SX25, SX26, SX27, SX28, SX29, SX30, SX31, SX32, SX33, SX34, SX35, SX36, SX37, SX38, SX39, SX40, SX41, SX42, SX43, SX44, SX45, SX46, SX47, SX48, SX49, SX50, SX51, SX52, SX53, SX54, SX55, SX56, SX57, SX58, SX59, SX60: PIN; PTH_39MIL
T1: MCP1825S; SOT-223
X1: MINI-USB; MOLEX_SD-67503-010

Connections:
GND: C1.2, C2.2, C3.2, C4.2, C5.2, C9.2, C10.2, C11.2, C12.2, K1.4 (VSS), K1.31 (VSS), K1.47 (VSS), K2.5 (VREFL), K2.6 (VSS), R4.1, R8.1, S1.3, S1.4 (3), SX32.1, SX42.1, SX50.1, SX53.1, SX55.1, SX60.1, T1.2 (GND), T1.PAD, X1.5, X1.P$1 (CASE), X1.P$2 (CASE), X1.P$3 (CASE), X1.P$4 (CASE), X1.P$5 (CASE), X1.P$6 (CASE)
unnamed: K2.7 (PTA3), SX59.1
unnamed: K1.22 (PTA0), K2.16 (PTB0), SX58.1
unnamed: K1.24 (PTA2), K2.17 (PTB1)
unnamed: C10.1, G1.1, K1.32 (PTA18)
unnamed: C11.1, G1.2, K1.33 (PTA19)
unnamed: G2.2 (1), K1.19 (XTAL32)
unnamed: G2.1 (2), K1.20 (EXTAL32)
unnamed: K2.18 (PTB2), S1.1, S1.2 (1), SX40.1
unnamed: K1.5 (USB0_DP), R6.2
unnamed: C8.1, K1.17 (VREF_OUT)
unnamed: K1.34 (RESET_B), K2.8 (PTA4), K2.25 (PTB5), SX38.1, SX56.1
unnamed: C7.1, K1.14 (VREFH), R3.2, SX16.1
unnamed: K1.6 (USB0_DM), R5.2
unnamed: C6.1, K1.13 (VDDA), R2.1, R3.1
unnamed: R6.1, X1.3
unnamed: R5.1, X1.2
unnamed: C3.1, R1.1, X1.1
unnamed: K1.23 (PTA1), K2.10 (PTA6), X1.4
unnamed: K1.45 (PTC2), SX5.1
unnamed: K1.44 (PTC1), SX6.1
unnamed: K1.63 (PTD6), SX7.1
unnamed: K1.62 (PTD5), SX8.1
unnamed: K1.37 (PTB2), SX9.1
unnamed: K1.38 (PTB3), SX10.1
unnamed: K1.36 (PTB1), SX11.1
unnamed: K1.35 (PTB0), SX13.1
unnamed: K1.43 (PTC0), SX15.1
unnamed: K1.58 (PTD1), SX17.1
unnamed: K1.50 (PTC5), P1.+, SX18.1
unnamed: K1.52 (PTC7), SX19.1
unnamed: K1.51 (PTC6), SX20.1
unnamed: K1.49 (PTC4), SX21.1
unnamed: K1.46 (PTC3), SX22.1
unnamed: K1.60 (PTD3), SX23.1
unnamed: K1.59 (PTD2), SX24.1
unnamed: K1.61 (PTD4), SX25.1
unnamed: K1.64 (PTD7), SX26.1
unnamed: K1.29 (PTA13), SX27.1
unnamed: K1.28 (PTA12), SX28.1
unnamed: K1.57 (PTD0), SX29.1
unnamed: K1.40 (PTB17), SX30.1
unnamed: K1.39 (PTB16), SX31.1
unnamed: K1.12 (ADC0_DM3), SX33.1
unnamed: K1.26 (PTA4), SX35.1
unnamed: K1.41 (PTB18), SX36.1
unnamed: K1.1 (PTE0), SX37.1
unnamed: K1.56 (PTC11), SX39.1
unnamed: K1.55 (PTC10), SX41.1
unnamed: K1.53 (PTC8), SX43.1
unnamed: P1.-, R8.2
unnamed: C6.2, C7.2, C8.2, K1.15 (VREFL), K1.16 (VSSA), R4.2, SX3.1
unnamed: K1.18 (DAC0), SX52.1
unnamed: K1.11 (ADC0_DP3), SX51.1
unnamed: K1.27 (PTA5), SX49.1
unnamed: K1.42 (PTB19), SX48.1
unnamed: K1.2 (PTE1), SX47.1
unnamed: K1.54 (PTC9), SX45.1
unnamed: C1.1, SJ1.2, SX2.1, T1.1 (IN)
unnamed: R7.2, SX46.1
unnamed: K1.10 (ADC0_DM0), SX12.1
unnamed: K1.9 (ADC0_DP0), SX14.1
unnamed: R1.2, SJ1.1, SX1.1
unnamed: C9.1, K1.21 (VBAT), R7.3
unnamed: C2.1, C4.1, C5.1, C12.1, K1.3 (VDD), K1.7 (VOUT33), K1.30 (VDD), K1.48 (VDD), K2.3 (VDD), K2.4 (VREFH), R2.2, R7.1, SX4.1, SX34.1, SX44.1, SX54.1, T1.3 (OUT)
unnamed: K1.25 (PTA3), K2.15 (PTA7), SX57.1

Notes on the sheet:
VIN
AGND
3.3V
23 / A9
22 / A8
21 / A7
20 / A6
19 / A5
18 / A4
17 / A3
16 / A2
15 / A1
14 / A0
13 (LED)
GND
A13
A12
DAC / A14
VBAT
RESET
PROG
A11
A10
AREF
VUSB
SWD
SWC
EN'

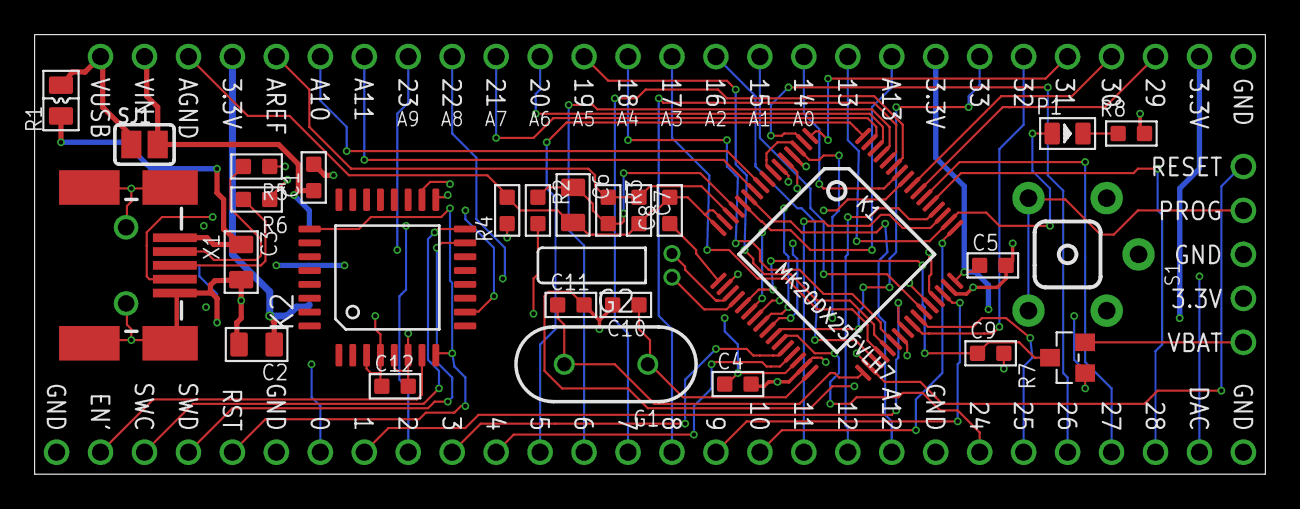
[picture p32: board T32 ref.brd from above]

Board: 4 copper layers, 71.1 x 25.4 mm, 89 parts (1 on the bottom side), 66 nets.

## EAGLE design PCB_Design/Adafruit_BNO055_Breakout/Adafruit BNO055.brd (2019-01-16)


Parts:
C1, C2: 22pF; 0805-NO
C3: 0.1uF; 0805-NO
C4: 0.1uF; 0805_10MGAP
C5: 10uF; 0805-NO
C6: 10uF; 0805_10MGAP
D1: 1n4148; SOD-323
FID1, FID2: FIDUCIAL""; FIDUCIAL_1MM
JP1: HEADER-1X676MIL; 1X06_ROUND_76
JP2: HEADER-1X476MIL; 1X04_ROUND_76
Q1, Q2: BSS138; SOT23-WIDE
R3, R4, R5, R6, R7, R10: 10K; 0805-NO
R8, R9: 10K; _0805MP
U1: MIC5225-3.3; SOT23-5
U$2: BNO055
U$29, U$30, U$31, U$32: MOUNTINGHOLE2.5_THICK; MOUNTINGHOLE_2.5_PLATED_THICK
Y1: 32.768kHz; CRYSTAL_8X3.8

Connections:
3.3V: C4.2, C6.1, JP1.2, Q1.1 (G), Q2.1 (G), R6.2, R7.2, R10.2, U1.5 (OUT), U$2.3 (VDD), U$2.4 (NBOOT_LOAD_PIN), U$2.28 (VDDIO)
5.0V: C5.1, JP1.1, R8.2, R9.2, U1.1 (IN), U1.3 (EN)
GND: C1.1, C2.1, C3.1, C4.1, C5.2, C6.2, JP1.3, R3.2, R4.2, R5.2, U1.2 (GND), U$2.2 (GND), U$2.10 (PIN10(GND)), U$2.15 (PIN15(GND)), U$2.16 (PIN16(GND)), U$2.18 (COM2(GND)), U$2.25 (GND)
I2CADDR_3V: JP2.4, R5.1, U$2.17 (COM3/I2C_ADDR)
INT_3V: JP2.3, U$2.14 (INT)
unnamed: C1.2, U$2.27 (XIN32), Y1.P$4 (2)
unnamed: C2.2, U$2.26 (XOUT32), Y1.P$1 (1)
unnamed: C3.2, U$2.9 (CAP)
NRESET_3V: D1.A, R10.1, U$2.11 (NRESET)
PS0_3V: JP2.1, R3.1, U$2.6 (PS0)
PS1_3V: JP2.2, R4.1, U$2.5 (PS1)
RST_5V: D1.C, JP1.6
SCL_3V: Q2.2 (S), R7.1, U$2.19 (COM1/SCL/RX)
SCL_5V: JP1.5, Q2.3 (D), R9.1
SDA_3V: Q1.2 (S), R6.1, U$2.20 (COM0/SDA/TX)
SDA_5V: JP1.4, Q1.3 (D), R8.1



Board: 2 copper layers, 26.7 x 20.3 mm, 31 parts (2 on the bottom side), 16 nets.

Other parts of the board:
U$3: PCBFEAT-REV-040
U$28: ADAFRUIT_TEXT_20MM
U$33: ADAFRUIT_2.5MM

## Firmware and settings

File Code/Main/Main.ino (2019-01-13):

#include <Wire.h>
#include <Adafruit_Sensor.h>
#include <Adafruit_BNO055.h>
#include <utility/imumaths.h>
#include <SPI.h>
#include <SD.h>
#include <math.h>
#include <EEPROM.h>
#include <PWMServo.h>

#define LOGGING_FREQUENCY 100.0
#define MAX_LOG_NUMBER 850

/* TODO: 
 *    SPEED UP the SD writing! (WRITE TO MEMORY DURING FLIGHT THEN COMPILE ALL DATA INTO A CSV AFTER LANDING?!!!)
 *    ADD Throw detection and find the initial velocity direction!
 *    ADD PID Control???
 *    TEST servo movement direction in opposing positions!
 */

const int chipSelect = BUILTIN_SDCARD;

PWMServo myservo;  // create servo object to control a servo
File dataFile;

Adafruit_BNO055 bno = Adafruit_BNO055(55);

adafruit_bno055_offsets_t calibrationData;

String rootFile = "datLOG";
int fileIndex = 0;

imu::Vector<3> upwardsVector(0.0,0.0,1.0);
imu::Vector<3> forwardsVector(1.0,0.0,0.0);
imu::Vector<3> gravityVec(0.0,0.0,-1.0);

class ControlObject { //contains all the needed info on a planet
public:
    imu::Vector<3> euler,gravity,lin_acc,initialThrowDirection; // initDir must be a unit vector!
    imu::Quaternion quat;
    double throwEulerHeading; // SET ON DEFINITION OF initialThrowDirection! (only calculate once) 
    double errorAngle;
    double controlSetpoint = 0.0;
    unsigned long curTime = millis();
    int numberLogs = 0;
    double updateTime = (1.0/LOGGING_FREQUENCY)*1000.0;
    const int rotation_direction = 1;

    //TODO: Add PID Parameters
    const double kPID = 2.0;
    
    void printErrorTerm();
    void logState();
    void updateState();
    void serialData();
    void gravityAngles();
    void PIDCalcAndSend();
    void calcEulerHeadingOffset();
    bool timeToLog(); 
      
};

void ControlObject::serialData() {
  String timeData = String("Time: "+String(this->curTime)+"\n");
  String eulerData = String("Euler: "+this->euler.toString()+"\n");
  String gravityData = String("Gravity: "+this->gravity.toString()+"\n");
  String linAccData = String("Linear Acceleration: "+this->lin_acc.toString()+"\n");
  String controlSetpointData = String("Setpoint: "+String(this->controlSetpoint)+"\n");
  String errorValueData = String("Error Angle: "+String(this->errorAngle)+"\n");

  String totalResult = String(timeData+eulerData+gravityData+linAccData+controlSetpointData+errorValueData);
  Serial.print(totalResult);
}

void ControlObject::updateState() {
  // Update internal class variables
  this->euler = bno.getVector(Adafruit_BNO055::VECTOR_EULER); // NOT BEING USED
  this->quat = bno.getQuat();
  this->gravity = bno.getVector(Adafruit_BNO055::VECTOR_GRAVITY); // NOT BEING USED
  this->lin_acc = bno.getVector(Adafruit_BNO055::VECTOR_LINEARACCEL); // NOT BEING USED

  imu::Vector<3> rot_state_vert = this->quat.rotateVector(upwardsVector);
  imu::Vector<3> rot_state_horiz = this->quat.rotateVector(forwardsVector);

  // Calculate error in tilt perpendicular to the direction of original throw
  imu::Vector<3> projRotOntoPlane = (rot_state_vert - (this->initialThrowDirection)*(rot_state_vert.dot(this->initialThrowDirection)));
  imu::Vector<3> projGravOntoPlane = (gravityVec - this->initialThrowDirection*(gravityVec.dot(this->initialThrowDirection)));
  double magAB = projRotOntoPlane.magnitude()*projGravOntoPlane.magnitude();
  double thetaFromCos = acos( (projRotOntoPlane.dot(projGravOntoPlane))/(magAB));
  //       sin(theta) = ((normal X a) dot b)/(mag a * mag b)
  double sinTheta = (((this->initialThrowDirection.cross(projGravOntoPlane)).dot(projRotOntoPlane))/magAB);
  double tiltError;
  
  if (sinTheta >= 0.0) {
      tiltError = (thetaFromCos - PI);
  } else {
      tiltError = (PI - thetaFromCos);
  }
  //Serial.println(tiltError);
  // –––––––––––––––––––––––––––––––––––––––––––––––––––––––

  // Calculate error in heading so that corrections can be made in the correct phase
  imu::Vector<3> projHeadingOntoXY = (rot_state_horiz - (upwardsVector)*(rot_state_horiz.dot(upwardsVector)));
  double magHeading = projHeadingOntoXY.magnitude();
  double thetaFromCosHeading = acos( (projHeadingOntoXY.dot(forwardsVector))/(magHeading));
  double sinThetaHeading = (((upwardsVector.cross(forwardsVector)).dot(projHeadingOntoXY))/magHeading);
  double headingAngle;
  if (sinThetaHeading >= 0.0) {
      headingAngle = (thetaFromCosHeading);
  } else {
      headingAngle = (2.0*PI - thetaFromCosHeading);
  }
  double directionalScalar = cos( headingAngle - this->throwEulerHeading );
  //Serial.println(directionalScalar);
  // –––––––––––––––––––––––––––––––––––––––––––––––––––––––

  this->errorAngle = ( this->controlSetpoint - (tiltError*directionalScalar*(this->rotation_direction)) ); //Push the correct result to class
  
}

void ControlObject::printErrorTerm() {
  Serial.println(String((this->errorAngle)*(this->kPID)));
}

void ControlObject::calcEulerHeadingOffset() {
  imu::Vector<3> xyPlane(0.0,0.0,1.0);
  imu::Vector<3> throwProjOntoXY = (this->initialThrowDirection - (xyPlane)*(this->initialThrowDirection.dot(xyPlane)));

  double magAB2 = throwProjOntoXY.magnitude();
  double thetaFromCos2 = acos( (throwProjOntoXY.dot(forwardsVector))/(magAB2));

  //       sin(theta) = ((normal X a) dot b)/(mag a * mag b) 
  double sinTheta2 = (((xyPlane.cross(forwardsVector)).dot(throwProjOntoXY))/magAB2);

  if (sinTheta2 >= 0.0) {
      this->throwEulerHeading = thetaFromCos2;
  } else {
      this->throwEulerHeading = (2.0*PI-thetaFromCos2);
  }
  
  // Serial.println(this->throwEulerHeading);

  // TODO: SET THE ROTATION DIRECTION TOO! (Somehow)
  
}

void ControlObject::logState() {
  this->curTime = millis();
  
  String timeData = String(this->curTime);
  String eulerData = String(this->euler.toString());
  String gravityData = String(this->gravity.toString());
  String linAccData = String(this->lin_acc.toString());
  String controlSetpointData = String(this->controlSetpoint);
  String errorValueData = String(this->errorAngle);

  String totalResult = String(timeData+","+eulerData+","+gravityData+","+linAccData+","+controlSetpointData+","+errorValueData);
  dataFile.println(totalResult);
  dataFile.flush();
  this->numberLogs = this->numberLogs + 1;
    
}

bool ControlObject::timeToLog() {
  return ( (this->numberLogs < MAX_LOG_NUMBER) && ((millis()-(this->curTime)) > updateTime) );
}

void ControlObject::PIDCalcAndSend() {
  int servoControl = map( (this->errorAngle)*(this->kPID), -PI, PI, 0, 180);
  int writeToServo = constrain(servoControl, 0, 180);
  myservo.write(writeToServo);
}

void loadSensorCalib() {
  int eeAddress = 0;
  long bnoID;

  EEPROM.get(eeAddress, bnoID);
  adafruit_bno055_offsets_t calibrationData;
  sensor_t sensor;
  /*
  *  Look for the sensor's unique ID at the beginning oF EEPROM.
  *  This isn't foolproof, but it's better than nothing.
  */
  bno.getSensor(&sensor);
  if (bnoID != sensor.sensor_id)
  {
      Serial.println("\nNo Calibration Data for this sensor exists in EEPROM");
      delay(500);
  }
  else
  {
      Serial.println("\nFound Calibration for this sensor in EEPROM.");
      eeAddress += sizeof(long);
      EEPROM.get(eeAddress, calibrationData);
      bno.setSensorOffsets(calibrationData);

      Serial.println("\n\nCalibration data loaded into BNO055");
  }
}

void printSystemInfo() {

  /* IT DOESNT LIKE THIS:
  Main:208: warning: 'self_test_result' is used uninitialized in this function 
  Main:208: warning: 'system_error' is used uninitialized in this function 
  */
  
  uint8_t *system_status;
  uint8_t *self_test_result;
  uint8_t *system_error;

  bno.getSystemStatus(system_status, self_test_result, system_error);
  Serial.println("ACC SELF TESTS TO FOLLOW:");
  Serial.println(*system_status,HEX);
  Serial.println(*self_test_result,BIN);
  Serial.println(*system_status,HEX);
}


ControlObject control_obj;


//––––––––––––––––––––––––––––––––––––––––––––––––––––––––––––––––––––––––––––


void setup() {
  pinMode(LED_BUILTIN , OUTPUT);

  Serial.begin(115200);
  if(!bno.begin()){
    Serial.println("Ooops, no BNO055 detected ... Check your wiring or I2C ADDR!");
    while(1);}
    
  loadSensorCalib();

  bno.setExtCrystalUse(true);
  bno.setMode(Adafruit_BNO055::OPERATION_MODE_M4G); // Because the gyroscope saturates at just over 5 RPS (2000 deg/s)

  printSystemInfo();
  
  if (!SD.begin(chipSelect)) {
    Serial.println("Card failed, or not present");
    while (1){
        digitalWrite(LED_BUILTIN, HIGH);
        delay(500);
        digitalWrite(LED_BUILTIN, LOW);
        delay(500);}} 
  else {
    Serial.println("Card initialized!");
  }

  while ( SD.exists( (rootFile+String(fileIndex)+String(".csv")).c_str() ) ) {
    fileIndex += 1;}
  
  Serial.println((rootFile+String(fileIndex)+String(".csv")).c_str());
  
  
  dataFile = SD.open( (rootFile+String(fileIndex)+String(".csv")).c_str() , O_WRITE | O_CREAT);
  
  if (dataFile) {
    dataFile.println("Time,Euler_yaw,Euler_roll,Euler_pitch,Grav_x,Grav_y,Grav_z,LinAcc_x,LinAcc_y,LinAcc_z,Control_Setpoint,Error_Angle");
  } else {
    Serial.println("Data file failed to open... :(");
    while (1) {
      digitalWrite(LED_BUILTIN, HIGH);
      delay(500);
      digitalWrite(LED_BUILTIN, LOW);
      delay(500);
     }
    }

  // FOR TESTING PURPOSES!
  control_obj.initialThrowDirection.x() = 1.0;
  control_obj.initialThrowDirection.y() = 0.0;
  control_obj.initialThrowDirection.z() = 0.0;

  // FOR TESTING PURPOSES!
  control_obj.calcEulerHeadingOffset();

   myservo.attach(30, 1000, 2000);

  digitalWrite(LED_BUILTIN, HIGH);
  
}

void loop() {
  control_obj.updateState();
  //Serial.println(control_obj.curTime - millis());
  control_obj.printErrorTerm();
  control_obj.PIDCalcAndSend();
  
  if (control_obj.timeToLog()) {
      //Serial.println("LOGGING!");
      control_obj.logState();
      //control_obj.serialData();
  }
}

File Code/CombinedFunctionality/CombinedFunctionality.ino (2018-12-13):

#include <Wire.h>
#include <Adafruit_Sensor.h>
#include <Adafruit_BNO055.h>
#include <utility/imumaths.h>
#include <PWMServo.h>
#include <SPI.h>
#include <SD.h>


Sd2Card card;
SdVolume volume;
SdFile root;

PWMServo servo;  // create servo object to control a servo
Adafruit_BNO055 bno = Adafruit_BNO055(55); 

const int SERVO_PIN = 30 //Teensy PWM Pin

void dataLog(imu::Vector<3> euler,imu::Vector<3> gravity,imu::Vector<3> lin_acc) {
  
}

void setup() {
  pinMode(LED_BUILTIN , OUTPUT);
  servo.attach(SERVO_PIN); // some motors need min/max setting (second and third argument)

  Serial.begin(9600);
  if(!bno.begin()){
    Serial.print("Ooops, no BNO055 detected ... Check your wiring or I2C ADDR!");
    while(1);}
    
  bno.setExtCrystalUse(true);
  bno.setMode(Adafruit_BNO055::OPERATION_MODE_M4G); // Because the gyroscope saturates at just over 5 RPS
  
}

void loop() {
  imu::Vector<3> euler = bno.getVector(Adafruit_BNO055::VECTOR_EULER);
  imu::Vector<3> gravity = bno.getVector(Adafruit_BNO055::VECTOR_GRAVITY);
  imu::Vector<3> lin_acc = bno.getVector(Adafruit_BNO055::VECTOR_LINEARACCEL);
  //myservo.write(pos); // 0 to 180 degrees
}

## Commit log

2018-11-26 Continuning to add pre-existing content
    [Body.SLDPRT, Control_surface_v2.sldprt, Frisbee_with_control_cutout.SLDPRT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]
2018-11-26 updating current content
2018-11-29 fixing references
    [Top_level_assembly.SLDASM]
2018-11-29 new CAD models
    [Frisbee_with_control_cutout_linear_v2.SLDPRT, Top_level_assembly.SLDASM, Top_level_assembly_v2.SLDASM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]
2018-12-05 Teensy code updates.
2018-12-06 Added more trial data and updated the logging script
    [DATALOG0.CSV, DATALOG1.CSV, DATALOG2.CSV]
2018-12-07 updated CAD
    [Frisbee_with_control_cutout_linear_v2.SLDPRT, Top_level_assembly_v2.SLDASM, Unaltered_disc.SLDPRT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]
2018-12-09 Added circuit schematics
2018-12-11 Updated main code to reflect a more realistic error value
    [MainV2.ino]
2018-12-11 Adding the most recent modified sensor libraries
2018-12-13 Adding more local CAD files
    [500mAh Battery.SLDASM, Adafruit_BNO055.SLDPRT, Battery Cell.sldprt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]
2018-12-13 CAD Changes
    [Frisbee_with_control_cutout_linear_v2.SLDPRT, Top_level_assembly_v2.SLDASM, linear_control_surface_v1.sldprt]
2018-12-14 Updating cad models
    [500mAh Battery.SLDASM, Adafruit_BNO055.SLDPRT, ControlHorn.sldprt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]
2019-01-12 Adding balanced electronics container draft to be 3d printed.
    [500mAh Battery.SLDASM, Adafruit_BNO055.SLDPRT, ControlHorn.sldprt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]
2019-01-12 Enclosure updates
    [ElectronicsEnclosure.sldprt, TopLevelAllComponents.SLDASM]
2019-01-12 nearly finalized enclosure
    [ElectronicsEnclosure.sldprt, TopLevelAllComponents.SLDASM]
2019-01-12 A few final changes
    [ElectronicsEnclosure.sldprt, TopLevelAllComponents.SLDASM]
2019-01-12 cosmetic tweak
    [TopLevelAllComponents.SLDASM, Top_level_assembly_v2.SLDASM]
2019-01-13 Final switch dim update
    [ElectronicsEnclosure.sldprt, ElectronicsEnclosureTEST.STL, TopLevelAllComponents.SLDASM]
2019-01-16 Added PCB design files.
    [Adafruit BNO055.brd, Adafruit BNO055.sch, Adafruit PowerBoost 1000C Rev B.brd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]

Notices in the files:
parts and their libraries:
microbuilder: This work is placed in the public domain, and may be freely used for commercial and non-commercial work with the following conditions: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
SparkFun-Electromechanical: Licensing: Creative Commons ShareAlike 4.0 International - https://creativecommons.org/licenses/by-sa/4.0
